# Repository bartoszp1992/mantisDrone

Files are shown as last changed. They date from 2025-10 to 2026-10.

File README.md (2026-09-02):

# Mantis repo

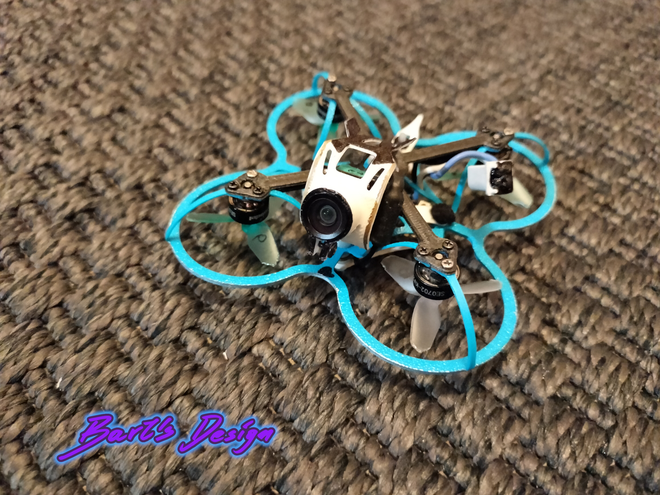
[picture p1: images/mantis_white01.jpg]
Mantis photo


**"Mantis" is 1.2" or 1.6" class printable freestyle/racing 1S tinywhoop**

# 3D printing
- **frame**
: PA12
- **ducts convertible**
: PC/PETG
- **canopy**
: PA12/TPU
- **FC cover**
: PA12
- **base**
: PC-CF/PETG-CF

# mechanical
- **base**
: printed basebase
- **frame**
: printed mantis frame
- **propellers**
: HQ Ultralight 3-Blade Propellers (1.0mm Shaft) or NBD Azi 3 blade. 31mm for 1.2" or 40mm for 1.6"
- **PA screws**
: 4x PA M2x20 screws
- **PA nuts**
: 4x PA M2 nuts
- **vibration isolators**
: 2x additional M2 vibration isolator for canopy mounts

# electronic
- **FC**
: BETAFPV Matrix 1S Brushless Flight Controller 5IN1/4IN1/3IN1
- **motors 1.2"**
: HAPPYMODEL SE0702 KV28000
- **motors 1.6"**
: BETAFPV 0802 Brushless Motors (2026) Racing/Freestyle
- **camera**
: CADDXFPV ant lite / BETAFPV C03(SD) or P1 air unit(HD)
> for SD: order also CADDXFPV Camera Accessories OSD Menu Board for ant lite camera, and switch video mode to PAL
- **batteries 1.2"**
: BETAFPV LAVA II 1S 280mAh 3.8V HV
- **batteries 1.6"**
: BETAFPV LAVA II 1S 480mAh 3.8V HV
- **charger**
: BETAFPV 6 Ports 1S Battery Charger (optionally with adapter)
- **cable**
: USB-C cable for communication
- **VTX**
: Foxeer reaper nano(only for SD 4in1)

# software
- **FC config**
: betaflight configurator

# tips
- put vibration isolator inside canopy tail mount
- put half of the cut-in vibration isolator as a pad for the front mount of the canopy

# firmware
If you are building remotely:
> choose analog OSD Protocol and type **OSD_HD** in custom defines, to build firmware with both- digital and analog OSD 
> In other options add **Magnetometers**, **Position Hold** and **Altitude Hold**

## notice
This repository includes third-party firmware binaries used by this FPV drone.

### Betaflight

Versions: 
- `2025.12.2`
- `2026.6.1`

Included firmware:

- `betaflight_2025.12.2_STM32G474_BETAFPVG473_ccb6e7f3.hex`
- `betaflight_2025.12.2_STM32G474_BETAFPVG473_V2_aa260427.hex`
- `betaflight_2026.6.1_STM32G474_BETAFPVG473_V2_d2c09b19.hex`

These firmware files were generated using the official Betaflight Cloud
Build service.

Flight controller targets:

- `BETAFPVG473`
- `BETAFPVG473_V2`

Additional build options used for this project:

- Analog OSD
- `OSD_HD`
- Magnetometers (`MAG`)
- Position Hold (`POSITION_HOLD`)
- Altitude Hold (`ALTITUDE_HOLD`)

No modifications were made to the Betaflight source code by this repository.
The options listed above are compile-time options supported by the official
Betaflight build system.

Corresponding source:

https://github.com/betaflight/betaflight
Tag corresponding to firmware version.

Betaflight is distributed under the GNU General Public License version 3.
A copy of the GNU GPL v3 is included in this repository as `LICENSE.txt`.

### Bluejay

Version: `v0.19.2`

Included firmware:

- `A_X_5_96_v0.19.2.hex`

This is an unmodified Bluejay firmware binary from the upstream
`v0.19.2` release.

Corresponding source:

Bluejay repository, tag `v0.19.2`.

Bluejay is distributed under the GNU General Public License version 3.
A copy of the GNU GPL v3 is included in this repository as `GPL-3.0.txt`.

### Copyright and attribution

Betaflight and Bluejay are independent open-source projects.
Copyright remains with their respective authors and contributors.

This repository does not claim ownership of Betaflight or Bluejay and is
not affiliated with or endorsed by either project.

[Betaflight](https://github.com/betaflight/betaflight/tree/2025.12.2)
[Betaflight](https://github.com/betaflight/betaflight/tree/2026.6.1)

[Bluejay](https://github.com/bird-sanctuary/bluejay/tree/v0.19.2)

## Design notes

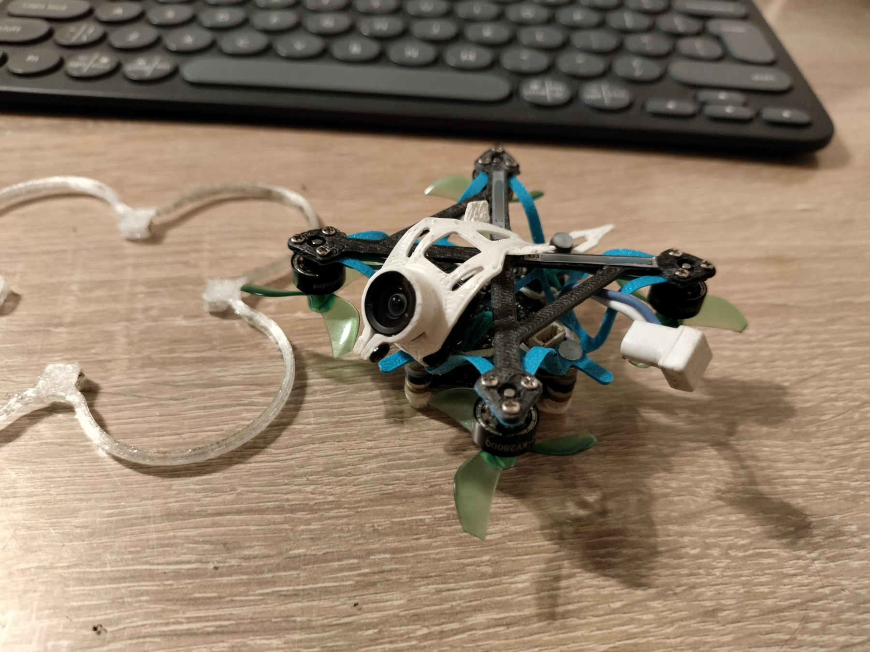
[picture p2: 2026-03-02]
images/convertible.jpg

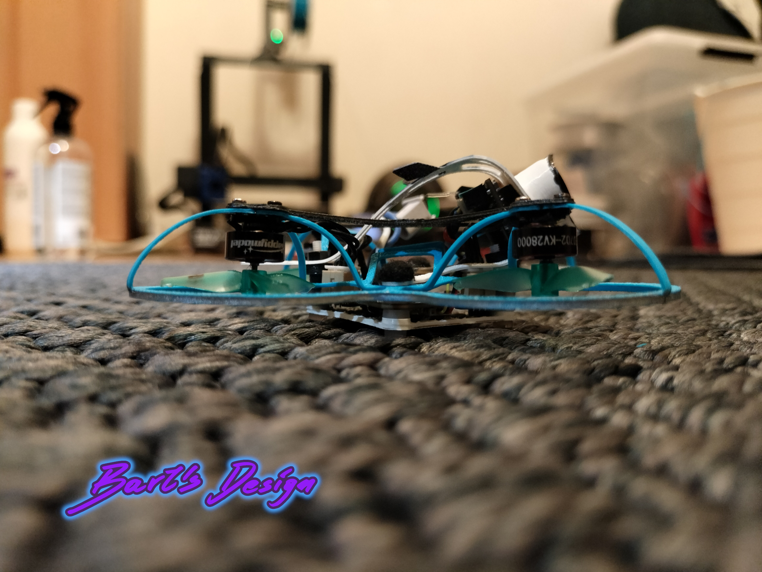
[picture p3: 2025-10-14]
images/mantis_white05.jpg

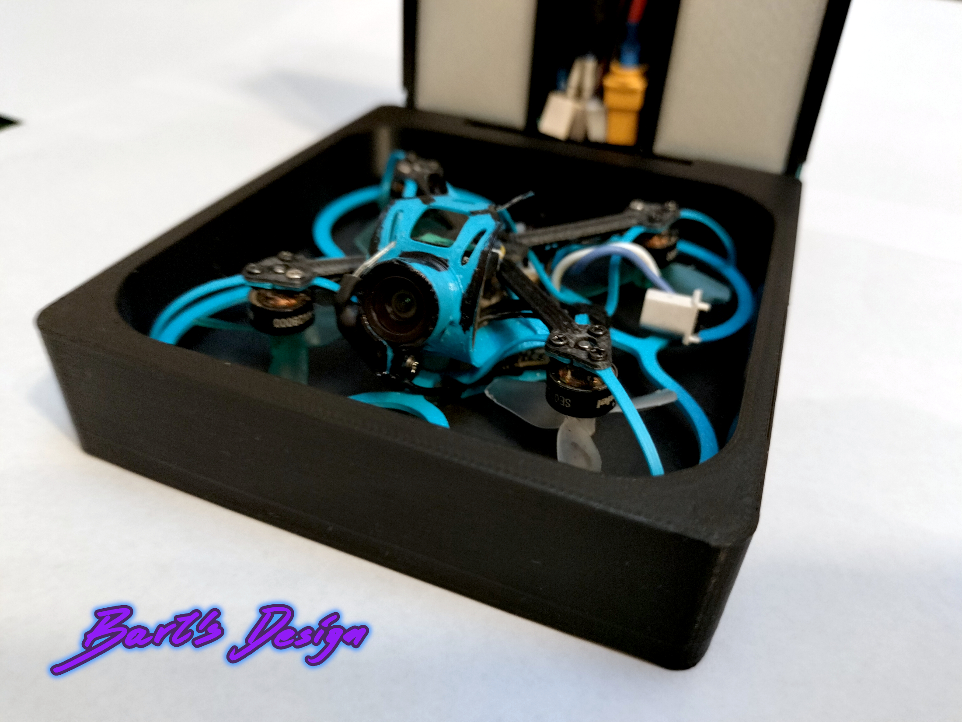
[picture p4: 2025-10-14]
images/mantis_blue03.jpg

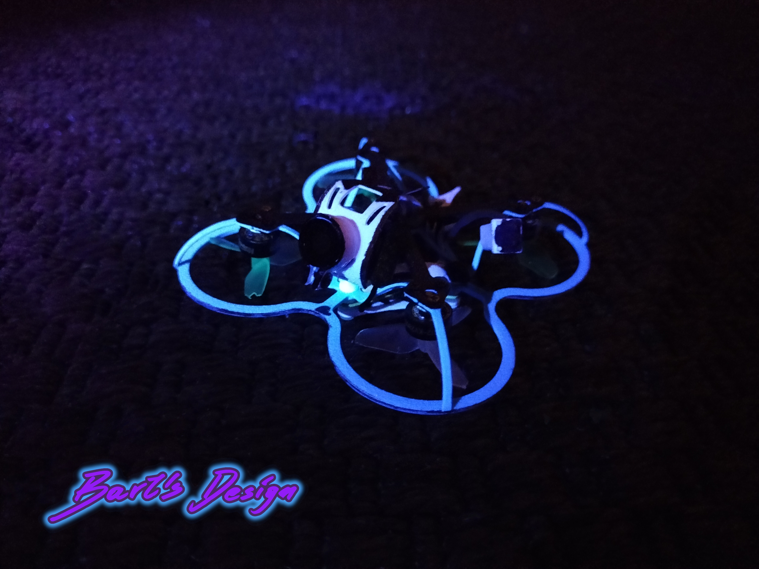
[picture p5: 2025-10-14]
images/mantis_white18.jpg

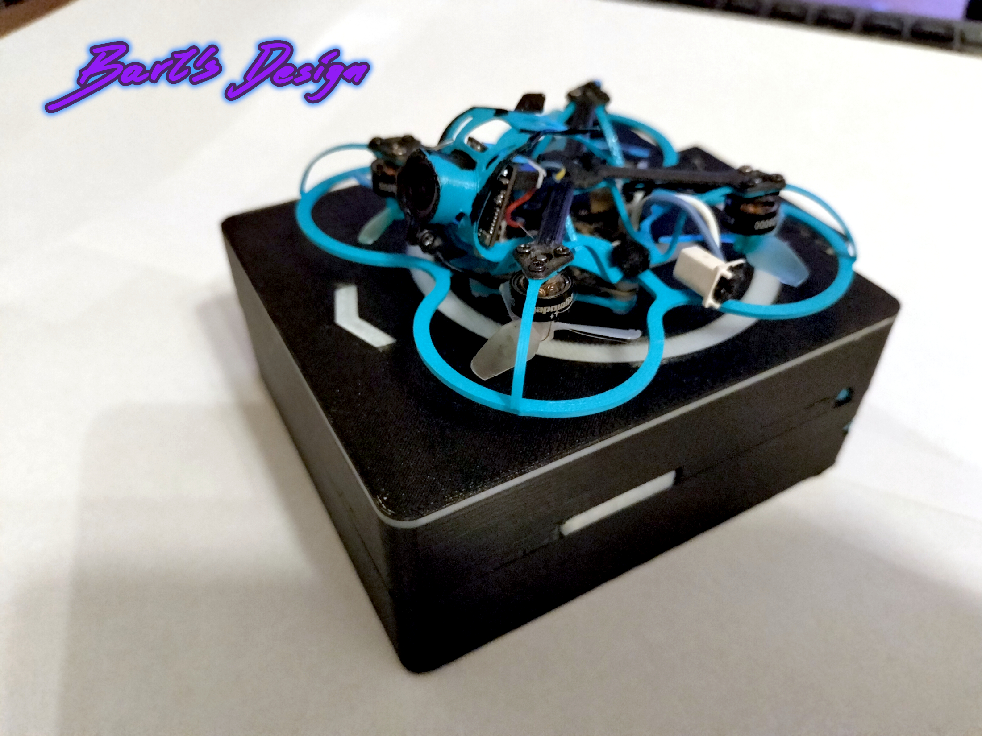
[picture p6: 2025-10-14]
images/mantis_blue10.jpg

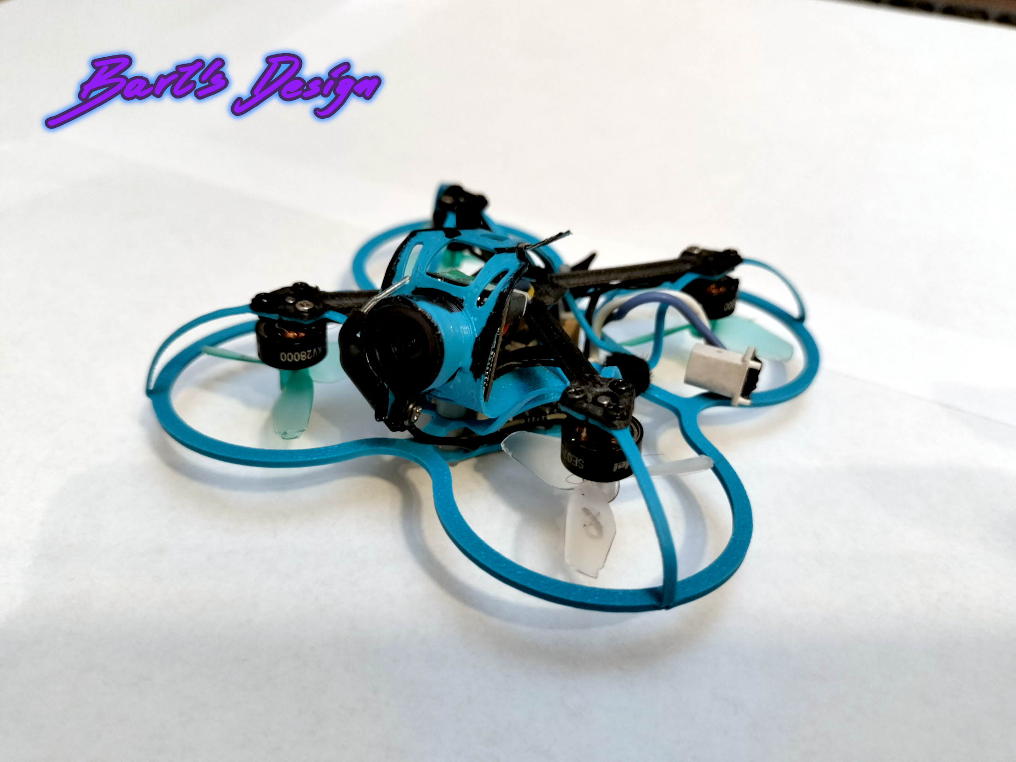
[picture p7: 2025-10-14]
images/mantis_blue04.jpg

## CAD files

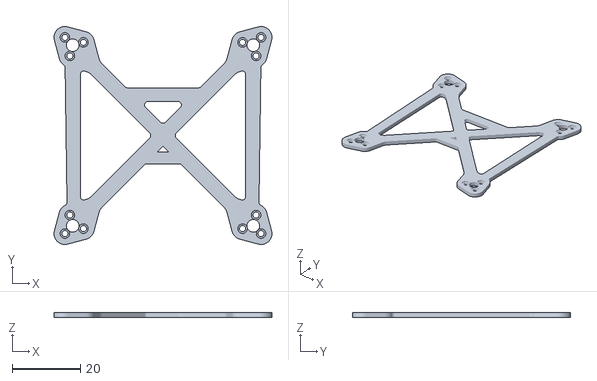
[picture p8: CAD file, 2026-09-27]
mechanical/output/parts.drone16-base15-R.stl
64.0 x 64.0 x 1.50

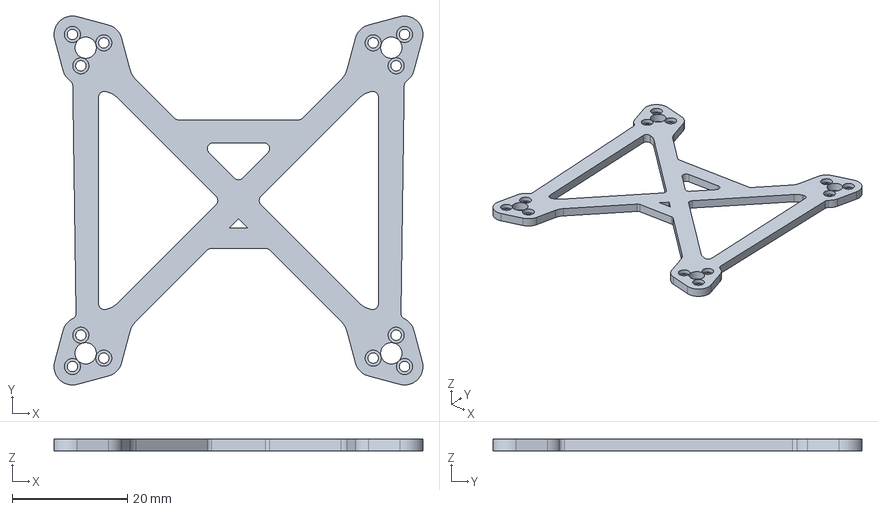
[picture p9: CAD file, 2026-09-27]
mechanical/parts/parts.drone16.FCStd
64.0 x 64.0 x 2.00 mm

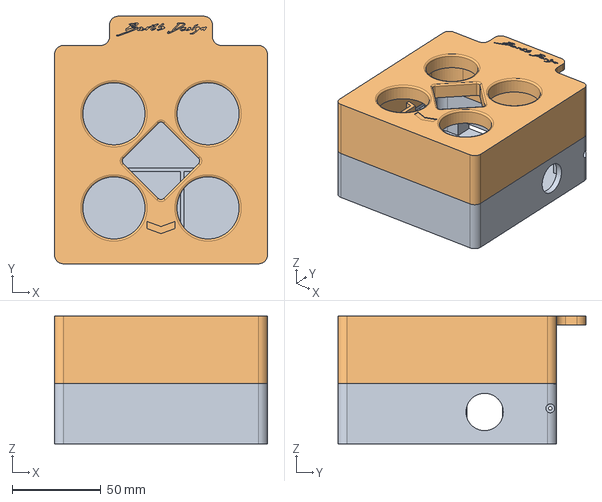
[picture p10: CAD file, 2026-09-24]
mechanical/parts/parts_box16.FCStd
120.0 x 139.5 x 72.0 mm
lid

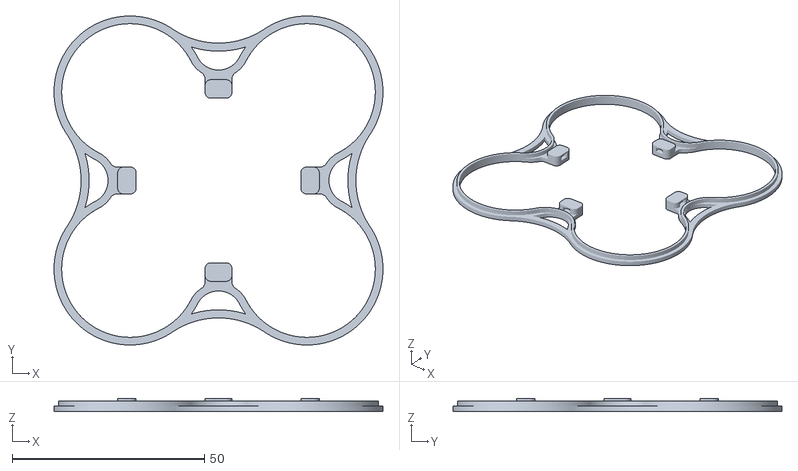
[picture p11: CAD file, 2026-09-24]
mechanical/output/parts.drone12-ducts-convertible.stl
85.5 x 85.5 x 3.40

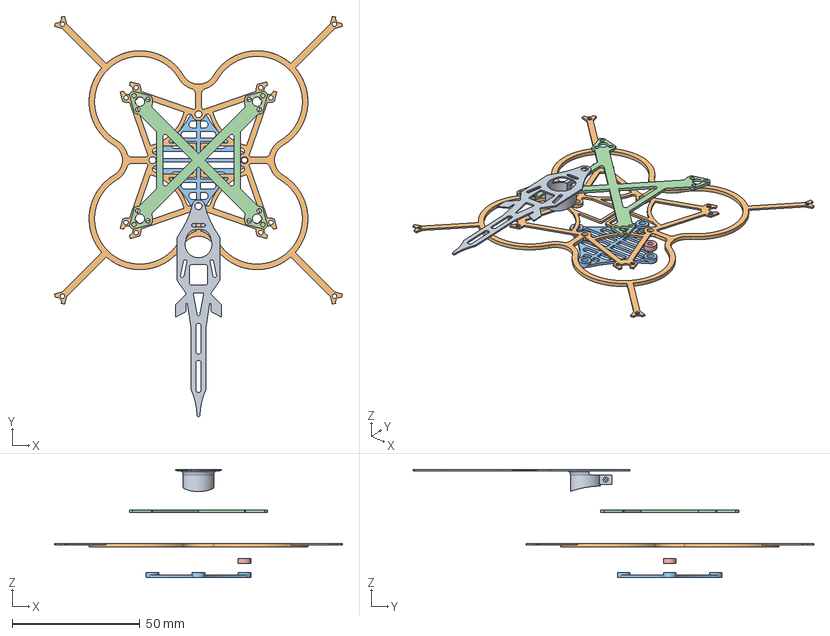
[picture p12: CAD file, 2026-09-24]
mechanical/parts/parts.drone12.FCStd
112.9 x 157.1 x 42.5 mm
canopy
frame-integral
FC cover
base10
sleeve 2mm

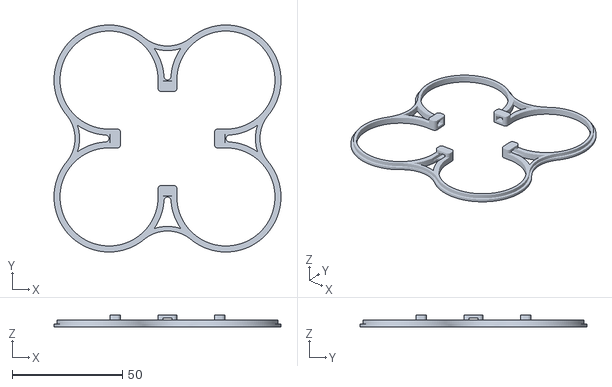
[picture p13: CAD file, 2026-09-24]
mechanical/output/parts.drone16-ducts-convertible.stl
103.0 x 103.0 x 5.40

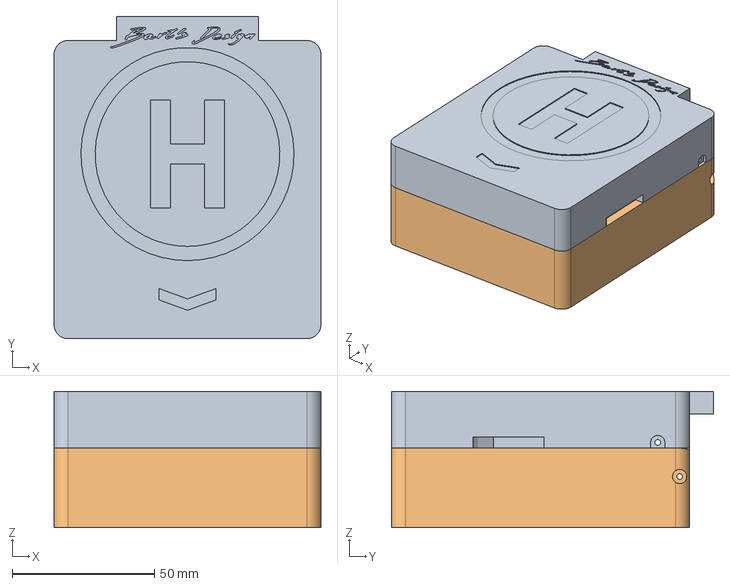
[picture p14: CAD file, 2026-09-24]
mechanical/parts/parts_box12.FCStd
94.0 x 113.5 x 48.0 mm
lid
box-HD

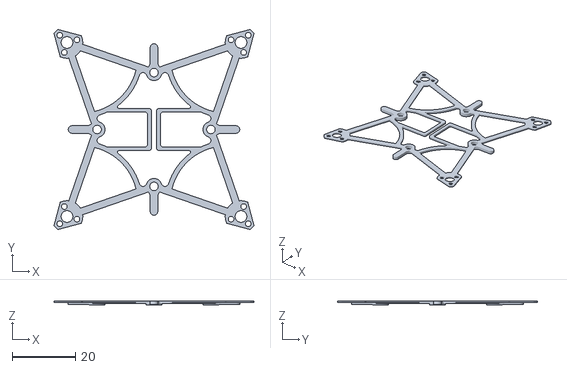
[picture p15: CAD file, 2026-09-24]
mechanical/output/parts.drone12-frame-convertible.stl
63.4 x 63.4 x 1.40

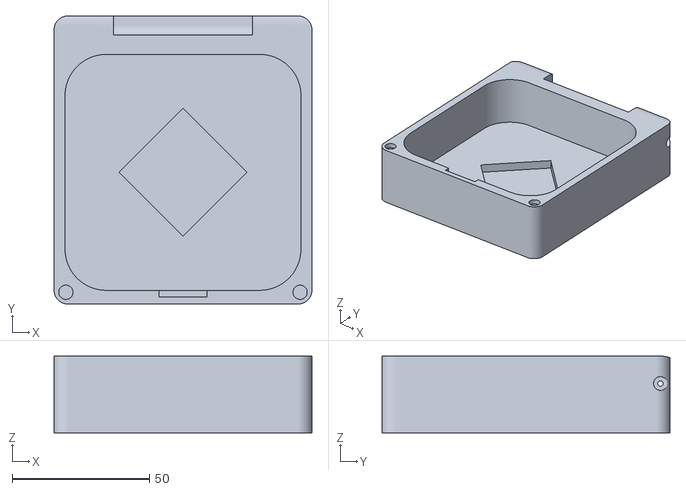
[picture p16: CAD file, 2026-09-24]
mechanical/output/parts_box12-box-HD.stl
94.0 x 105.0 x 28.0

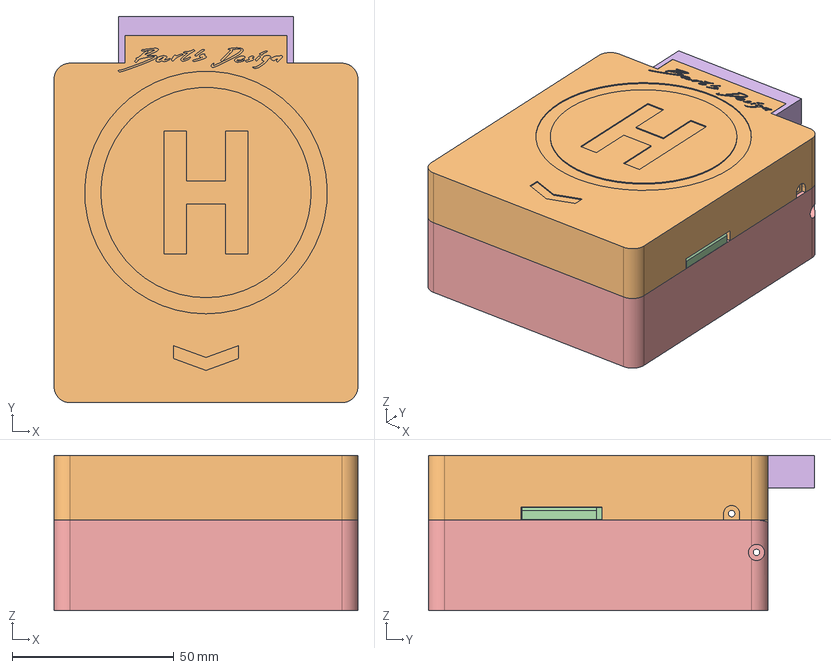
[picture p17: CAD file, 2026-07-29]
mechanical/parts/parts_box12_fc102.FCStd
94.0 x 119.5 x 48.0 mm
ring
lid
battery lid L
battery lid R
box-HD
lid-addon-HD

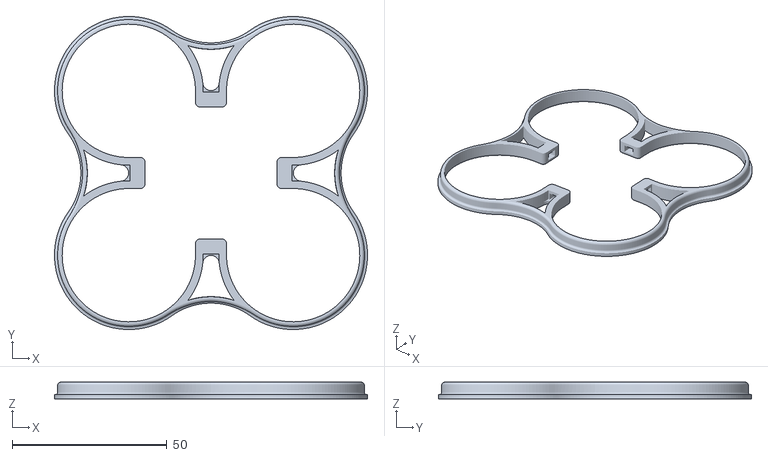
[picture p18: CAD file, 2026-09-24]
mechanical/output/parts.drone16-ducts-convertible2.stl
101.0 x 101.0 x 5.40

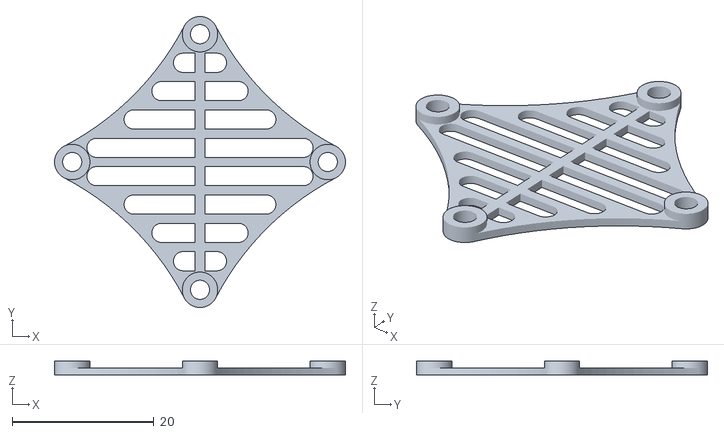
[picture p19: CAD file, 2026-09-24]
mechanical/output/parts.drone12-FC cover.stl
41.1 x 41.1 x 2.00

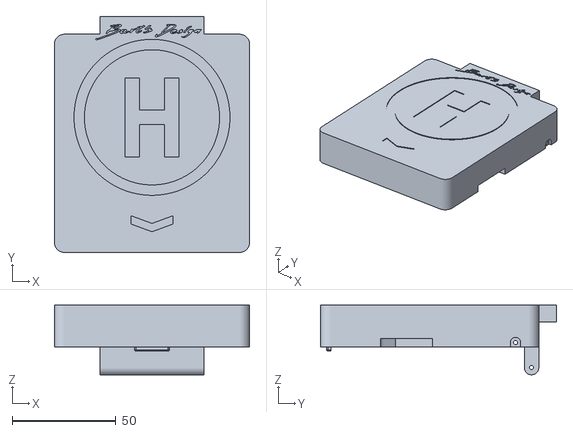
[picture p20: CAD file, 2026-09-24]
mechanical/output/parts_box12-lid.stl
94.0 x 113.5 x 33.5

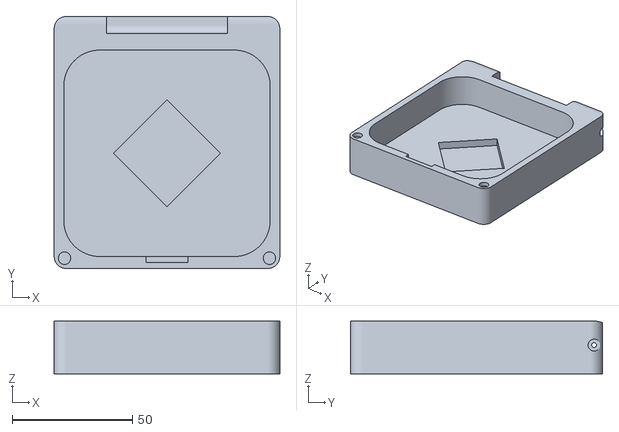
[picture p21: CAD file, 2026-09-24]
mechanical/output/parts_box12-box.stl
94.0 x 105.0 x 22.0

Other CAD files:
mechanical/output/parts.drone16-base20-R.stl
mechanical/parts/parts_box16_fc102.FCStd
mechanical/output/parts.drone12-base08.stl
mechanical/output/parts_box16-box.stl
mechanical/output/parts.drone12-FC cover-UL.stl
mechanical/output/parts.drone12-base10.stl
mechanical/output/parts.drone12-base20-R.stl
mechanical/output/parts.drone12-canopy-UL.stl
mechanical/output/parts.drone12-canopy.stl
mechanical/output/parts.drone12-frame-convertible-R.stl
mechanical/output/parts.drone12-frame-integral.stl
mechanical/output/parts.drone12-sleeve 2mm.stl
mechanical/output/parts.drone16-frame-convertible-R.stl
mechanical/output/parts_box12-battery lid L.stl
mechanical/output/parts_box12-battery lid R.stl
mechanical/output/parts_box12-lid-addon-HD.stl
mechanical/output/parts_box12-ring.stl
mechanical/output/parts_box16-lid.stl

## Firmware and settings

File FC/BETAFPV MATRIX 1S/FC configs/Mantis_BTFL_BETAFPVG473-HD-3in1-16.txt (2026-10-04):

defaults nosave


# version
# Betaflight / STM32G47X (G473) 2025.12.2 Jul 30 2026 / 19:03:24 (79065c96b) MSP API: 1.47
# config rev: e378347

# start the command batch
batch start

# reset configuration to default settings
defaults nosave

board_name BETAFPVG473
manufacturer_id BEFH
mcu_id 001c00363235510f30303938
signature 

# name: BD2 "Mantis" HD

# feature
feature -AIRMODE
feature GPS
feature TELEMETRY
feature LED_STRIP
feature OSD

# serial
serial UART2 2 115200 57600 0 115200
serial UART4 131073 115200 57600 0 115200

# led
led 0 7,15::AB:0
led 1 8,15::AB:0

# mode_color
mode_color 6 0 11
mode_color 6 1 6

# aux
aux 0 0 1 1300 2100 0 0
aux 1 1 2 900 1300 1 0
aux 2 3 4 900 1300 1 0
aux 3 3 0 1700 2100 1 0
aux 4 6 7 900 1300 0 0
aux 5 27 4 1700 2100 1 0
aux 6 27 0 900 1300 1 0
aux 7 11 4 900 1300 1 0
aux 8 11 0 1700 2100 1 0
aux 9 15 6 1700 2100 0 0
aux 10 28 2 900 1700 0 0
aux 11 35 4 1700 2100 1 0
aux 12 35 0 1700 2100 1 0
aux 13 39 3 1700 2100 1 0
aux 14 49 7 1700 2100 0 0

# master
set gyro_lpf1_static_hz = 0
set dyn_notch_q = 750
set gyro_lpf1_dyn_min_hz = 0
set gyro_lpf1_dyn_max_hz = 650
set acc_trim_pitch = 6
set acc_trim_roll = 1
set acc_calibration = -82,9,5,1
set fpv_mix_degrees = 20
set blackbox_sample_rate = 1/1
set blackbox_disable_rc = ON
set blackbox_disable_bat = ON
set blackbox_disable_mag = ON
set blackbox_disable_alt = ON
set blackbox_disable_rssi = ON
set blackbox_disable_attitude = ON
set dshot_bidir = ON
set motor_pwm_protocol = DSHOT300
set motor_poles = 12
set motor_output_reordering = 3,1,2,0,4,5,6,7
set failsafe_delay = 10
set failsafe_throttle = 1250
set failsafe_switch_mode = STAGE2
set failsafe_procedure = GPS-RESCUE
set align_board_roll = 180
set align_board_yaw = 180
set bat_capacity = 425
set vbat_max_cell_voltage = 440
set vbat_min_cell_voltage = 310
set vbat_warning_cell_voltage = 340
set ibata_scale = 550
set ibata_offset = -100
set 3d_deadband_low = 1400
set 3d_deadband_high = 1600
set 3d_neutral = 1500
set small_angle = 180
set gps_rescue_alt_mode = CURRENT_ALT
set gps_rescue_initial_climb = 2
set gps_rescue_allow_arming_without_fix = ON
set pos_hold_without_mag = ON
set ledstrip_rainbow_freq = 102
set osd_warn_bitmask = 270329
set osd_cap_alarm = 1900
set osd_tim1 = 5120
set osd_tim2 = 5121
set osd_vbat_pos = 449
set osd_link_quality_pos = 3149
set osd_tim_2_pos = 7213
set osd_flymode_pos = 2584
set osd_g_force_pos = 2080
set osd_throttle_pos = 3181
set osd_crosshairs_pos = 4409
set osd_ah_sbar_pos = 6458
set osd_ah_pos = 6330
set osd_current_pos = 2529
set osd_mah_drawn_pos = 6529
set osd_craft_name_pos = 6144
set osd_pilot_name_pos = 7176
set osd_gps_speed_pos = 6584
set osd_gps_lon_pos = 65
set osd_gps_lat_pos = 81
set osd_gps_sats_pos = 1549
set osd_home_dir_pos = 7459
set osd_home_dist_pos = 1485
set osd_flight_dist_pos = 1453
set osd_compass_bar_pos = 6166
set osd_altitude_pos = 5613
set osd_power_pos = 289
set osd_warnings_pos = 14838
set osd_avg_cell_voltage_pos = 14400
set osd_battery_usage_pos = 2561
set osd_disarmed_pos = 6614
set osd_core_temp_pos = 2466
set osd_stick_overlay_left_pos = 129
set osd_stick_overlay_right_pos = 149
set osd_sys_goggle_voltage_pos = 129
set osd_stat_bitmask = 397246
set osd_profile = 2
set system_hse_mhz = 0
set debug_mode = FFT_FREQ
set rpm_filter_harmonics = 1
set craft_name = BD2 "Mantis" HD
set pilot_name = Bart SQ5SAZ
set ap_hover_throttle = 1420
set ap_throttle_max = 1850

profile 0

# profile 0
set profile_name = ducts
set dterm_lpf1_dyn_min_hz = 86
set dterm_lpf1_dyn_max_hz = 172
set dterm_lpf1_static_hz = 86
set dterm_lpf2_static_hz = 172
set d_pitch = 31
set d_roll = 33
set d_max_roll = 44
set d_max_pitch = 43
set dyn_idle_min_rpm = 25
set simplified_d_gain = 110
set simplified_pitch_d_gain = 85
set simplified_dterm_filter_multiplier = 115

profile 1

# profile 1
set profile_name = open
set dterm_lpf2_static_hz = 350
set p_pitch = 35
set i_pitch = 64
set d_pitch = 25
set f_pitch = 106
set p_roll = 40
set i_roll = 72
set p_yaw = 40
set i_yaw = 72
set d_max_pitch = 34
set dyn_idle_min_rpm = 25
set simplified_pi_gain = 90
set simplified_pitch_d_gain = 75
set simplified_pitch_pi_gain = 85
set simplified_dterm_filter = OFF

profile 2

profile 3

# restore original profile selection
profile 0

rateprofile 0

rateprofile 1

rateprofile 2

rateprofile 3

# restore original rateprofile selection
rateprofile 0

# save configuration

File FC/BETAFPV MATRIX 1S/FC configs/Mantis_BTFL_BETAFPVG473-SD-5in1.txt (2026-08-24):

defaults nosave


# version
# Betaflight / STM32G47X (G473) 2025.12.4 Aug 24 2026 / 18:50:07 (c2af58a0c) MSP API: 1.47
# config rev: 1359bbe

# start the command batch
batch start

# reset configuration to default settings
defaults nosave

board_name BETAFPVG473_V2
manufacturer_id BEFH
mcu_id 000100273235510935303333
signature 

# name: BD2 "MANTIS"

# feature
feature -AIRMODE
feature TELEMETRY
feature LED_STRIP
feature OSD

# led
led 0 7,15::AB:11
led 1 8,15::AB:11

# color
color 7 208,0,255
color 11 271,125,255
color 13 269,0,255

# mode_color
mode_color 6 0 12
mode_color 6 1 6

# aux
aux 0 0 1 1300 2100 0 0
aux 1 1 2 900 1300 1 0
aux 2 6 7 900 1300 0 0
aux 3 15 6 1700 2100 0 0
aux 4 28 2 900 1700 0 0
aux 5 35 4 1700 2100 1 0
aux 6 39 3 1700 2100 1 0
aux 7 49 7 1700 2100 0 0

# vtxtable
vtxtable bands 5
vtxtable channels 8
vtxtable band 1 BOSCAM_A A CUSTOM  5865 5845 5825 5805 5785 5765 5745 5725
vtxtable band 2 BOSCAM_B B CUSTOM  5733 5752 5771 5790 5809 5828 5847 5866
vtxtable band 3 BOSCAM_E E CUSTOM  5705 5685 5665 5645 5885 5905 5925 5945
vtxtable band 4 FATSHARK F CUSTOM  5740 5760 5780 5800 5820 5840 5860 5880
vtxtable band 5 RACEBAND R CUSTOM  5658 5695 5732 5769 5806 5843 5880 5917
vtxtable powerlevels 5
vtxtable powervalues 1 2 3 4 0
vtxtable powerlabels 25 100 200 400 PIT

# master
set dyn_notch_count = 0
set dyn_notch_q = 500
set acc_trim_pitch = 6
set acc_calibration = -82,9,5,1
set fpv_mix_degrees = 40
set blackbox_sample_rate = 1/2
set motor_idle = 580
set dshot_bidir = ON
set motor_pwm_protocol = DSHOT300
set motor_output_reordering = 3,1,2,0,4,5,6,7
set failsafe_delay = 10
set failsafe_throttle = 1250
set align_board_roll = 180
set align_board_yaw = 225
set bat_capacity = 250
set vbat_max_cell_voltage = 435
set ibata_scale = 550
set ibata_offset = -100
set 3d_deadband_low = 1400
set 3d_deadband_high = 1600
set 3d_neutral = 1500
set small_angle = 180
set gps_ublox_use_galileo = ON
set pid_process_denom = 2
set ledstrip_rainbow_freq = 102
set osd_warn_bitmask = 270333
set osd_cap_alarm = 400
set osd_vbat_pos = 2433
set osd_link_quality_pos = 2166
set osd_tim_2_pos = 6230
set osd_flymode_pos = 6606
set osd_g_force_pos = 6209
set osd_throttle_pos = 2200
set osd_crosshairs_pos = 6381
set osd_ah_sbar_pos = 6382
set osd_ah_pos = 6254
set osd_current_pos = 2464
set osd_mah_drawn_pos = 6465
set osd_craft_name_pos = 6177
set osd_pilot_name_pos = 6193
set osd_gps_speed_pos = 364
set osd_gps_lon_pos = 65
set osd_gps_lat_pos = 81
set osd_gps_sats_pos = 407
set osd_home_dir_pos = 279
set osd_home_dist_pos = 407
set osd_flight_dist_pos = 375
set osd_compass_bar_pos = 74
set osd_altitude_pos = 407
set osd_power_pos = 289
set osd_warnings_pos = 14761
set osd_avg_cell_voltage_pos = 6241
set osd_battery_usage_pos = 2497
set osd_disarmed_pos = 6539
set osd_core_temp_pos = 2401
set osd_stick_overlay_left_pos = 129
set osd_stick_overlay_right_pos = 149
set osd_sys_goggle_voltage_pos = 129
set osd_stat_bitmask = 397246
set osd_profile = 2
set osd_displayport_device = AUTO
set vtx_band = 5
set vtx_channel = 4
set vtx_power = 1
set vtx_freq = 5769
set vcd_video_system = PAL
set displayport_max7456_blk = 2
set displayport_max7456_wht = 0
set craft_name = BD2 "MANTIS"
set pilot_name = Bart SQ5SAZ

profile 0

# profile 0
set throttle_boost = 25
set p_pitch = 32
set i_pitch = 58
set d_pitch = 13
set f_pitch = 87
set p_roll = 31
set i_roll = 56
set d_roll = 14
set f_roll = 84
set p_yaw = 31
set i_yaw = 56
set f_yaw = 84
set d_max_roll = 19
set d_max_pitch = 18
set simplified_master_multiplier = 70
set simplified_d_gain = 70
set simplified_pitch_d_gain = 80

profile 1

profile 2

profile 3

# restore original profile selection
profile 0

rateprofile 0

rateprofile 1

rateprofile 2

rateprofile 3

# restore original rateprofile selection
rateprofile 0

# save configuration

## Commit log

2025-07-15 update OSD layout
    [Mantis_BTFL_BETAFPVG473-MkI.txt]
2025-07-16 firmware changed to 4.5.1 becouse theres some problems with TBS Smart audio on 4.5.2 config update
    [Mantis_BTFL_BETAFPVG473-MkI.txt]
2025-07-16 add case
    [parts_mechanical-housing.stl, parts_mechanical-lid.stl, parts_mechanical.FCStd]
2025-07-17 add BOM better case lid add photo
    [parts_mechanical-housing.stl, parts_mechanical-lid.stl, parts_mechanical.FCStd]
2025-07-18 housing update
    [parts_mechanical-housing.stl, parts_mechanical-lid.stl, parts_mechanical.FCStd]
2025-07-22 add simple canopy removed mantis text from housing lid
    [mantis-canopy-simple.stl, mantis-canopy.FCStd, parts_mechanical-lid.stl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]
2025-07-22 canopy corrections
    [mantis-canopy-simple.stl, mantis-canopy.FCStd]
2025-07-23 housing renamed to box
    [parts_mechanical-box.stl, parts_mechanical-lid.stl, parts_mechanical.FCStd]
2025-08-01 FC config update
    [Mantis_BTFL_BETAFPVG473-MkI.txt]
2025-08-01 revert vbat_scale and ibata_scale
    [Mantis_BTFL_BETAFPVG473-MkI.txt]
2025-08-02 working on pushers canopy
    [mantis-canopy-puller.stl, mantis-canopy-pusher.stl, mantis-canopy-simple.stl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]
2025-08-02 reorganized, add FC cover
    [fccover-Body.stl, fccover.FCStd, mantis-canopy-puller.stl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]
2025-08-02 add stabilizer
    [fccover-Body.stl, fccover.FCStd, mantis-canopy-pusher.3mf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]
2025-08-02 pusher config
    [Mantis_BTFL_BETAFPVG473-MkI-puller.txt, Mantis_BTFL_BETAFPVG473-MkI-pusher.txt, mantis-canopy.FCStd]
2025-08-02 motor reorder
    [Mantis_BTFL_BETAFPVG473-MkI-pusher.txt]
2025-08-02 add sleeve
    [mantis-canopy-sleeve.stl, mantis-canopy.FCStd]
2025-08-02 smaller trim channel
    [mantis-canopy-pusher.stl, mantis-canopy.FCStd]
2025-08-02 remove sleeve 1mm FC cover
    [fccover-Body.stl, fccover.FCStd, mantis-canopy-sleeve.stl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]
2025-08-02 VTX config
    [Mantis_BTFL_BETAFPVG473-MkI-pusher.txt]
2025-08-02 update with call sign
    [Mantis_BTFL_BETAFPVG473-MkI-pusher.txt]
2025-08-04 update VTX power table
    [Mantis_BTFL_BETAFPVG473-MkI-pusher.txt]
2025-08-07 pusher2 canopy
    [mantis-canopy-pusher2.stl, mantis-canopy.FCStd]
2025-08-12 update stats
    [Mantis_BTFL_BETAFPVG473-MkI-pusher.txt]
2025-08-22 add thin canopy
    [mantis-canopy-pusher2 L.stl, mantis-canopy-pusher2 PA.stl, mantis-canopy-pusher2 R.stl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]
2025-08-22 thicker L variant
    [mantis-canopy-pusher2 L.stl, mantis-canopy.FCStd]
2025-09-11 removed lowrace
    [Mantis_BTFL_BETAFPVG473-MkI-pusher.txt]
2025-09-12 add LL canopy
    [mantis-canopy-pusher2 LL.stl, mantis-canopy.FCStd]
2025-09-12 LL canopy fixes
    [mantis-canopy-pusher2 LL.stl, mantis-canopy.FCStd]
2025-09-13 add tail support
    [mantis-canopy-tail support.stl, mantis-canopy.FCStd]
2025-09-13 tail support fix
    [mantis-canopy-tail support.stl, mantis-canopy.FCStd]
2025-09-15 remove mantis edgeTX model, add FPV model remap arm to SB
    [Mantis_BTFL_BETAFPVG473-MkI-pusher.txt]
2025-09-16 speed limit on SB
    [Mantis_BTFL_BETAFPVG473-MkI-pusher.txt]
2025-09-16 add expo
    [Mantis_BTFL_BETAFPVG473-MkI-pusher.txt]
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2025-09-20 reorganized, new bumblebee model
    [BTFL_cli_backup_20250715_205911_BETAFPVG473.txt, Mantis_BTFL_BETAFPVG473-MkI-puller.txt, Mantis_BTFL_BETAFPVG473-MkI-pusher.txt]
2025-10-04 changed rate
    [Mantis_BTFL_BETAFPVG473-MkI-pusher.txt]
2025-10-06 add lighter FC cover
    [fccover-Body.stl, fccover-light.stl, fccover-standard.stl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]
2025-10-06 box2 without hole
    [parts_mechanical-box2.stl, parts_mechanical.FCStd]
2025-10-06 add canopy emboss add wings OSD changes
    [Mantis_BTFL_BETAFPVG473-MkI-pusher.txt, mantis-canopy-pusher2 LL.stl, mantis-canopy.FCStd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]
2025-10-06 box base fix
    [parts_mechanical-box2.stl, parts_mechanical.FCStd]
2025-10-07 add new lid
    [assembly_mechanical.FCStd, parts_mechanical-battery lid (Mirror #1).stl, parts_mechanical-battery lid.stl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]
2025-10-07 remove old stl's
    [parts_mechanical-band.stl, parts_mechanical-screw.stl]
2025-10-07 lid fixes
    [parts_mechanical-battery lid L.stl, parts_mechanical-battery lid R.stl, parts_mechanical-lid3.stl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]
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2025-10-11 reversed frame
    [frame-frame.stl, frame.FCStd]
2025-10-11 wider motor base arms
    [frame-motor base.stl, frame.FCStd]
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2025-10-14 larger internal duct diameter canopy arm cut
    [frame-frame2.stl, frame.FCStd, mantis-canopy-pusher3.stl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]
2025-10-14 canopy and frame fixes
    [frame-frame2.stl, frame.FCStd, mantis-canopy-pusher3.stl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]
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2025-10-24 spoke fix
    [parts.drone-frame.stl, parts.drone.FCStd]
2025-10-24 spoke fix 2
    [parts.drone-frame.stl, parts.drone.FCStd]
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2025-11-28 add box lid positioning
    [parts_box-box.stl, parts_box-lid.stl, parts_box.FCStd]
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2025-12-27 motor base renamed to stiffener add bars
    [parts.drone-motor base.stl, parts.drone-stiffener.stl, parts.drone.FCStd]
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2026-01-05 mmono buttons swapped
    [Mantis_BTFL_BETAFPVG473-MkI-pusher.txt]
2026-01-05 air mode mono reverted
    [Mantis_BTFL_BETAFPVG473-MkI-pusher.txt]
2026-01-10 add ledlow on pocket
    [Mantis_BTFL_BETAFPVG473-MkI-pusher.txt]
2026-02-07 change crash flip switch
    [Mantis_BTFL_BETAFPVG473-MkI-pusher.txt]
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2026-02-10 lid addon fix
    [parts_box-lid-addon-HD.stl, parts_box.FCStd]
2026-02-10 box HD fixes
    [parts_box-box-HD.stl, parts_box.FCStd]
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2026-02-11 new configs, new firmware
    [Mantis_BTFL_BETAFPVG473-HD-4in1.txt, Mantis_BTFL_BETAFPVG473-SD-5in1.txt]
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2026-02-16 add 4in1 SD, readme update
    [Mantis_BTFL_BETAFPVG473-SD-4in1.txt]
2026-02-16 fix vtx config
    [Mantis_BTFL_BETAFPVG473-SD-4in1.txt]
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2026-02-20 add 1mm stiffener
    [parts.drone-stiffener.stl, parts.drone-stiffener08.stl, parts.drone-stiffener10.stl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]
2026-02-20 increased clearance of convertible frame mounts
    [parts.drone-ducts-convertible.stl, parts.drone.FCStd]
2026-02-21 airmode instead of horizon
    [Mantis_BTFL_BETAFPVG473-HD-4in1.txt]
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2026-02-23 add new duct for convertible
    [parts.drone-ducts-convertible.stl, parts.drone-ducts-convertible2.stl, parts.drone.FCStd]
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2026-03-30 add 3D, new channels config
    [Mantis_BTFL_BETAFPVG473-HD-4in1.txt, Mantis_BTFL_BETAFPVG473-SD-4in1.txt]
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2026-05-16 frame symmetry fix
    [parts.drone-frame-convertible.stl, parts.drone-frame-toothpick.stl, parts.drone-frame.stl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]
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2026-05-16 ducts fixes
    [parts.drone30.FCStd]
2026-05-17 before removing PA12 part
    [parts.drone30-base10.stl, parts.drone30-canopy.stl, parts.drone30-frame-convertible.stl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]
2026-05-17 new 30 frame, remove unnecessary parts
    [parts.drone12.FCStd, parts.drone30-base10.stl, parts.drone30-canopy.stl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]
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2026-05-17 readme update, thicker 30 frame
    [parts.drone30-frame80.stl, parts.drone30-rubber band clip.stl, parts.drone30.FCStd]
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2026-06-02 add save at end of config
    [Mantis_BTFL_BETAFPVG473-HD-4in1.txt, Mantis_BTFL_BETAFPVG473-SD-4in1.txt, Mantis_BTFL_BETAFPVG473-SD-5in1.txt]
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2026-06-09 remove HD config, remove 3D mode
    [Mantis_BTFL_BETAFPVG473-HD-4in1.txt, Mantis_BTFL_BETAFPVG473-SD-4in1.txt]
